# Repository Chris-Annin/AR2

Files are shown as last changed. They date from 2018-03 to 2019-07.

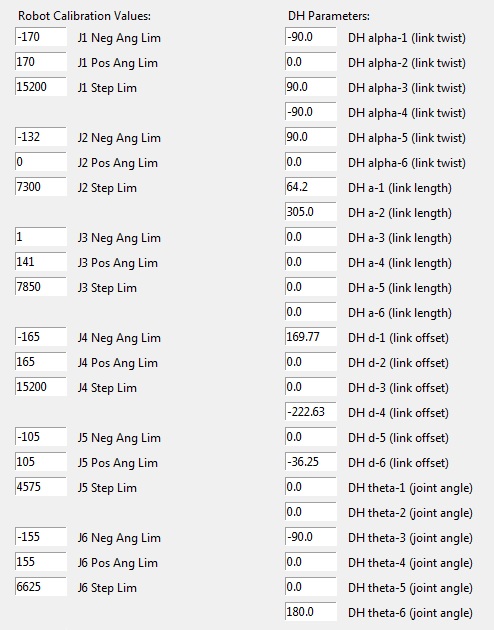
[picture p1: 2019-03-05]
RaspberryPi/default calibration values.jpg

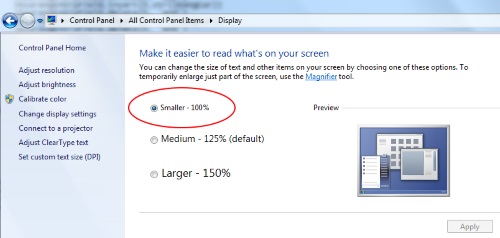
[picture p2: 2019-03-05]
RaspberryPi/display setting.jpg

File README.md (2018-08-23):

# AR2

## 6 axis stepper motor robot and control software

https://www.anninrobotics.com/

The AR2 is a small desktop robot that is modeled similar to an industrial 6 axis robot.  This is a DIY project that can be built from 3D printed components or from machined aluminum components, uses low cost stepper motors and arduino controller.

This project includes:

- Bill of materials and instructions
- CAD files to 3D print components to build the robot
- Arduino sketch for stepper driver control
- Software to program and operate robot
- Kinematic model

All geared stepper motors and drivers are available from  [www.omc-stepperonline.com](https://www.omc-stepperonline.com/?tracking=59c1139e8987b) and all other misc. hardware are off-the-shelf items available from multiple sources (see the bill of materials info within each manual).

(https://www.youtube.com/watch?v=EAcU4k2Qskk)

Startup & Calibration: [Calibration Video](https://youtu.be/MMESgfq2Mjg)

Programming: [Programming Video](https://youtu.be/BozgdjE-HR8)

How the math works: [Kinematic Videos](https://youtu.be/FIx6olybAeQ)

Please review all of the videos on programming and calibration,
I will try to answer as many emails as I can: chris.annin@gmail.com
#
Its important to me that this project is free and available to everyone but any donations that
can help with all that has gone into it would be hugely appreciated.  Thank you very much.


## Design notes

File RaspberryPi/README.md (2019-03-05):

# AR2 Raspberry Pi Source Files
Contributed by Zach Allen

This code is modified from the software version `2.1.5` so you can drive the AR2 Robot with a Raspberry Pi.  You can use a keyboard, mouse, and monitor with the RPi, or configure it as an access point and connect to it remotely from a tablet or phone using VNC Viewer.

### Prerequisites

Make sure you're using a complete version of Raspbian.  This has not been tested on other OS versions.  Find the latest Raspbian distribution at Raspberry Pi's [Download](https://www.raspberrypi.org/downloads/raspbian/) page.

## Getting Started and Installation

Once the files are on your Raspberry Pi, follow the links below to complete the set-up procedure.

1. Follow the [Configure RPi](ref/CONFIGURE.md) guide to clone the GitHub repository to your RPi and to properly set up the configuration settings for the following steps.
2. Follow the [Desktop Shortcut](ref/SHORTCUT.md) guide to add a clickable shortcut to your desktop to easily launch the program.
3. Follow the [Run-on-Boot](ref/RUN-ON-BOOT.md) guide to configure the program to launch automatically when you start the RPi.
4. Follow the [Access Point](ref/AP-SETUP.md) guide to set up your RPi to connect to it remotely, via a phone or tablet using VNC.

## Using the program

Plug the USB into the Raspberry Pi and the Arduino, give power to the Arduino and the AR2, and you will be all set to run the AR2 software.  Please see Chris's [documentation](https://www.anninrobotics.com/downloads) for using the software.

## Built With

* [Raspbian Stretch](https://www.raspberrypi.org/downloads/raspbian/) - The OS used

## Authors

* **Chris Annin** - *Initial work* - [Annin Robotics](https://www.anninrobotics.com/)
* **Zach Allen** - *Modifying software for RPi*

## Acknowledgments

* Huge kudos to Chris Annin for all the work he has done on the AR2, and for sharing it for free for others to learn and create!

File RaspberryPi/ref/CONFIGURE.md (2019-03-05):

# Set Up and Configure your Raspberry Pi
[Return to README.md](../README.md)

## Download Raspbian OS

If you are using a "fresh" Raspberry Pi, you'll need to get an OS on a Micro SD card to use the RPI.  Go to Raspberry Pi's [download](https://www.raspberrypi.org/downloads/raspbian/) page to get the latest Raspbian distribution for Raspberry Pi.  At the time of this writing, the OS is "Raspbian Stretch with desktop and recommended software".  This page also has instructions for writing the OS image to a Micro SD card as well.

## Boot up the Raspberry Pi

Once the OS image is copied onto the Micro SD card, insert the SD card into the RPi, connect a monitor, keyboard and mouse, and plug in 5V power with a micro USB.  The RPi will turn on automatically and begin installing the OS. Once booted, follow the on-screen set-up instructions.

### Configure Settings

Open the applications ("Start") menu and select `Preferences` and then `Raspberry Pi Configuration`.

On the `Interfaces` tab, make sure the following are marked as `Enabled`
* SSH
* VNC
* Serial Port
* Serial Console

If you will be using a tablet for remote control of the RPi, you can change the screen resolution accordingly on the `System` tab.  Once you change the resolution, you will be required to restart the RPi.

## Clone GitHub Repository

Open terminal and navigate to the `Documents` folder.
```
cd /home/pi/Documents/
```

Type the following command to clone the repository
```
git clone https://github.com/Chris-Annin/AR2.git
```

Once it has finished downloading, navigate down into the `RaspberryPi` folder
```
cd /AR2/RaspberryPi
```

The paths in the source code are mapped to this directory.  If you would prefer the source files to be located in a different directory, all of the paths in the `AR2.py` file must be updated. If anyone knows of a better way to use the relative path, please let me know and I'll update the files and this guide.

If you want to check that the program run, type the following command
```
python AR2.py
```

[Continue](./SHORTCUT.md) to create a desktop shortcut to run the program.

[Return to README.md](../README.md)

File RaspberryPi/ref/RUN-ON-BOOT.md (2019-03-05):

# Set up Raspberry Pi to run AR2 Program on Start Up
[Return to README.md](../README.md)

This guide will show you how to configure the RPI to run the AR2 program automatically when the RPi is booted.

First, open terminal.  The working directory is not important at this time.

Edit `/etc/profile` and add a command to run the program.
```
sudo nano /etc/profile
```
Scroll all the way to the bottom and add the following
```
sudo python /home/pi/Documents/AR2/RaspberryPi/AR2.py &
```

It is **critical** you have the ampersand (&) at the end, otherwise your Raspberry Pi will get stuck in a loop when booting.

Once you have added the command, save and exit, and reboot.
```
Ctrl+x
y
Enter
```
```
sudo reboot
```

Once the RPi has rebooted, the AR2 software screen should automatically run. Unless you close the program and need to re-open it, you shouldn't need to use the desktop shortcut.  However it's there anyway!

[Continue](./AP-SETUP.md) to learn how to configure your RPi for remote connection via VNC Viewer.

[Return to README.md](../README.md)

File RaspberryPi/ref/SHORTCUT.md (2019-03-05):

# Create Desktop shortcut
[Return to README.md](../README.md)

This guide will show you how to create a Desktop shortcut from which you can run the program.

Open a terminal window and point the directory to the Desktop
```
cd /home/pi/Desktop/
```

Create a new text file on the Desktop.  Since it does not yet exist, a new file will be automatically created.
```
sudo nano AR2.desktop
```

Type or copy/paste the following into the text file.  This will configure the details necessary to make it a desktop shortcut with an icon.
```
[Desktop Entry]
Name=AR2
Comment=AR2 Robot Control Program
Icon=/home/pi/Documents/AR2/RaspberryPi/AR2.ico
Exec=python /home/pi/Documents/AR2/RaspberryPi/AR2.py
Type=Application
Terminal=false
Categories=None;
```
Then, save and exit
```
Ctrl+x
y
Enter
```

Now, the shortcut should appear on your desktop!

If the shortcut hasn't appeared, reboot your Raspberry Pi.
```
sudo reboot
```

If that still doesn't work, check the spelling of everything and make sure the files are in the correct directory.

If you want the program to start up when you turn on the Raspberry Pi, continue on the [run-on-boot documentation](./RUN-ON-BOOT.md)

[Return to README.md](../README.md)

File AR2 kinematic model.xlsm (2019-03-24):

FORWARD KINAMATICS |  |  |  |  |  |  |  |  |  | INVERSE KINAMATICS
 | IN |  |  |  |  |  | OUT |  |  |  | IN
 | degrees | radians
J1 * ( -170 / 170 ) | 0.01 | 0.0001745329252 |  |  |  | X | 323.0799945 |  |  | X | 323.0799945 | J1 | 0.01
J2 * ( -132 / 0 ) | -90 | -1.570796327 |  |  |  | Y | 0.05638699285 |  |  | Y | 0.05638699285 | J2 | -90
J3 * ( 1 / 140 ) | 90 | 0 |  |  |  | Z | 474.7636732 |  |  | Z | 474.7636732 | J3 | 90
 | 0.01 | 0.0001745329252 |  |  |  | y | -89.98 | -1.570447261 |  | y | -89.98 | J4 | 0.01000000001 | 0.01000000001 | -179.99
 | 0.01 | 0.0001745329252 |  |  |  | p | 90.01 | 1.57097086 |  | p | 90.01 | J5 | 0.009999999984 | 0.009999999984 | -0.009999999984 |  | WRIST CONF. | "F"
 | 0.01 | 3.141767187 |  |  |  | r | -90.00999825 | -1.570970829 |  | r | -90.00999825 | J6 | 0.009999999994 | 0.009999999994 | -179.99 |  | QUADRANT | 1
 | DH params |  |  |  |  |  |  |  |  |  |  |  | CALCULATE J2 AND J3 ANGLE ( note that only arm forward and arm mid are used. Arm back config not used and elbow back is not used - to flip robot center of wrist "P" back past center line of J1 would require arm confuration paramaters be attached to each move command )
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

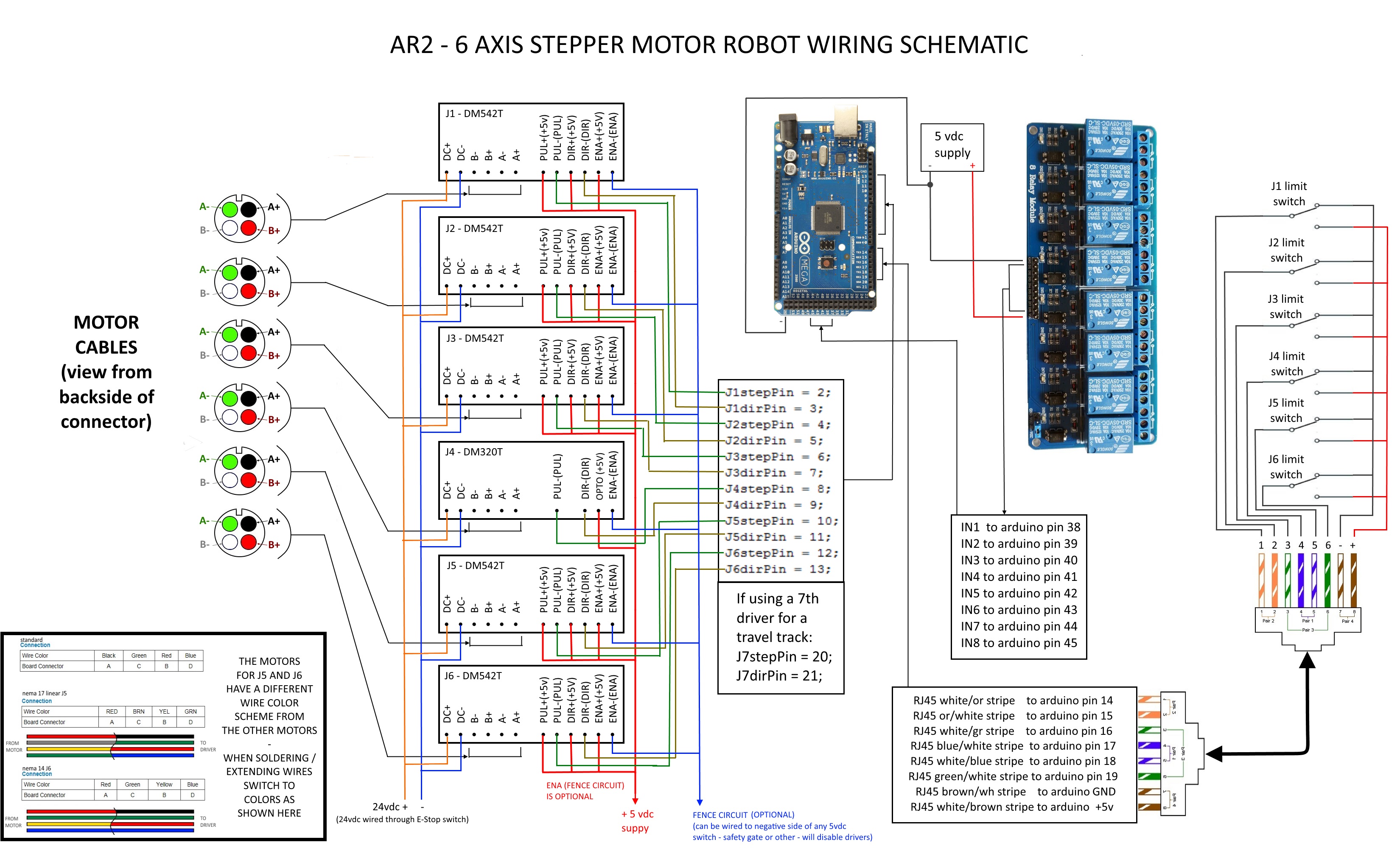
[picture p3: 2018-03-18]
Schematic.jpg

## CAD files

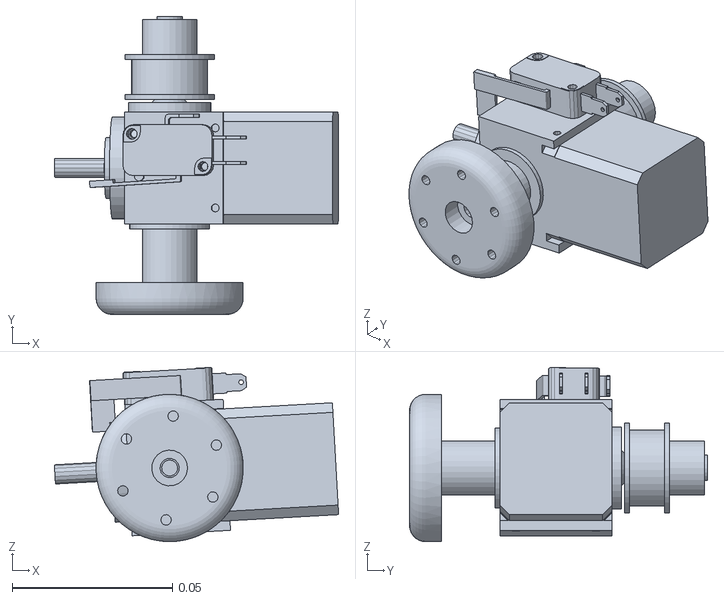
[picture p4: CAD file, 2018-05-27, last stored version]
AR2urdf/meshes/link_5.STL
0.0888 x 0.0931 x 0.0544

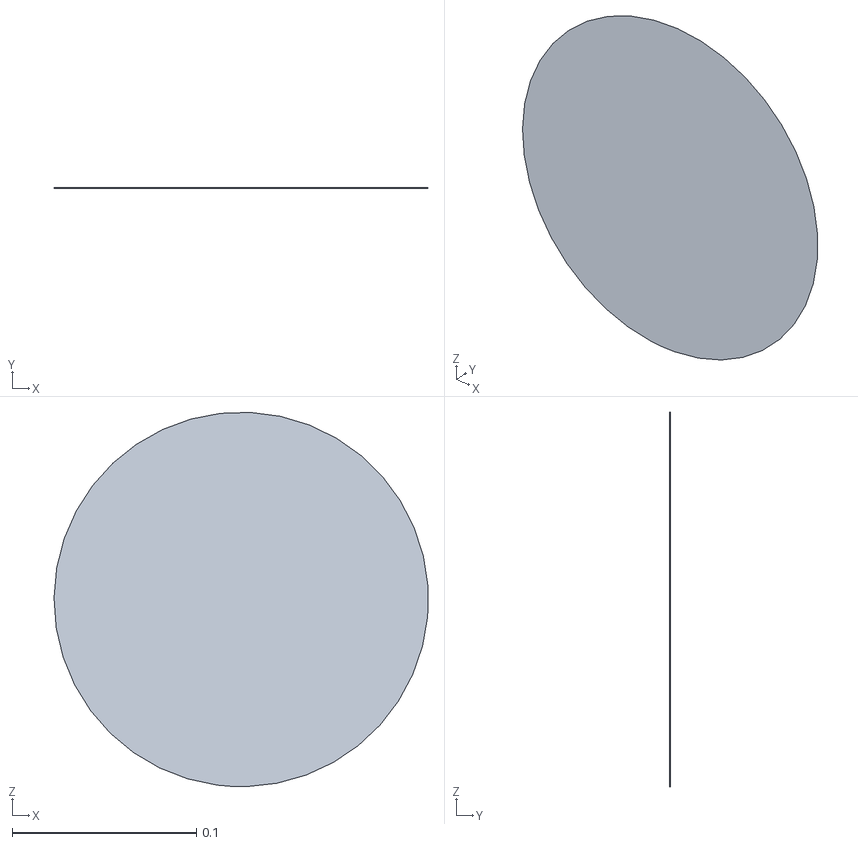
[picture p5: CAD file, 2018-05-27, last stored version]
AR2urdf/meshes/base_link.STL
0.203 x 0.000127 x 0.203

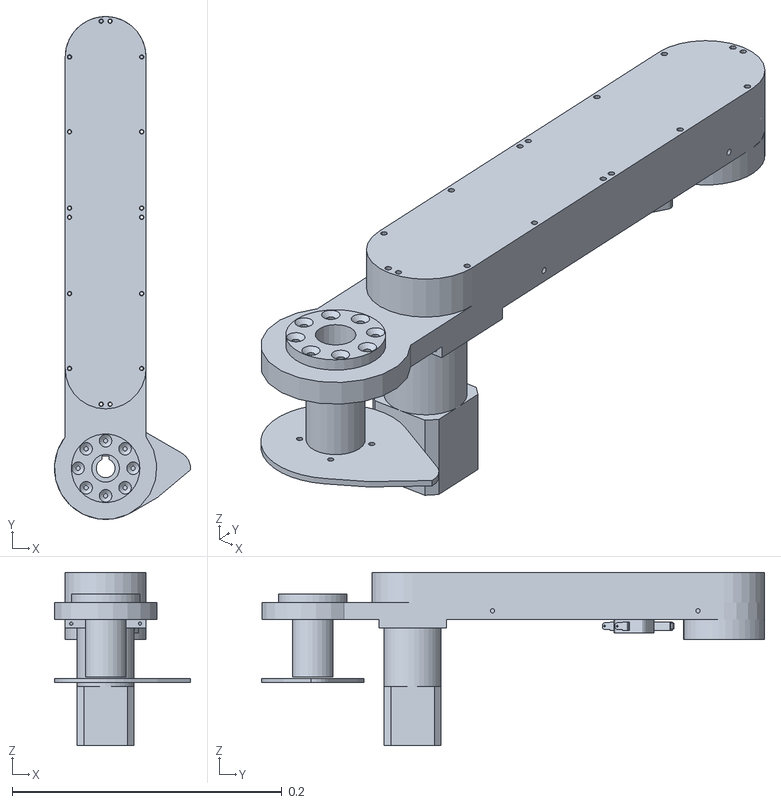
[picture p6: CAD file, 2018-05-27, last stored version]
AR2urdf/meshes/link_2.STL
0.101 x 0.373 x 0.129

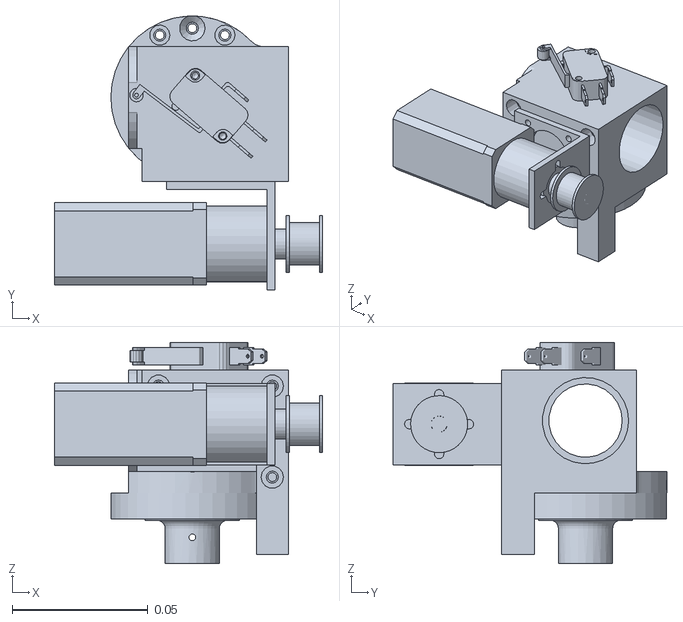
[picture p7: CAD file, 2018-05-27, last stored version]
AR2urdf/meshes/link_3.STL
0.0987 x 0.101 x 0.0816

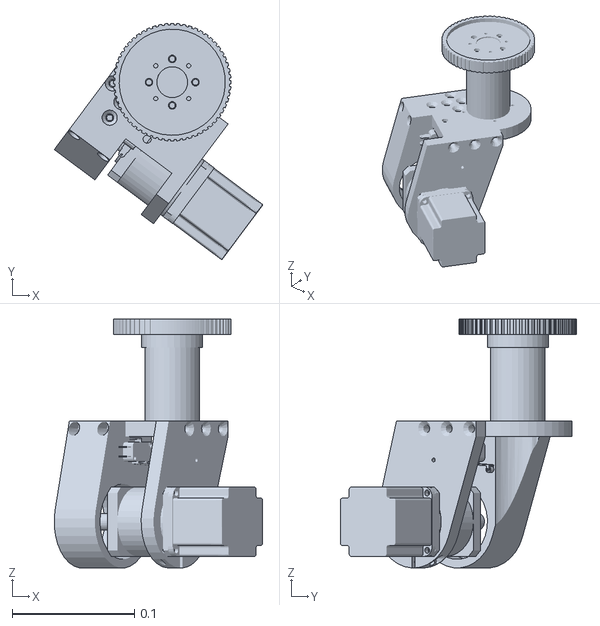
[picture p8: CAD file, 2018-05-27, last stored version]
AR2urdf/meshes/link_1.STL
0.171 x 0.194 x 0.204

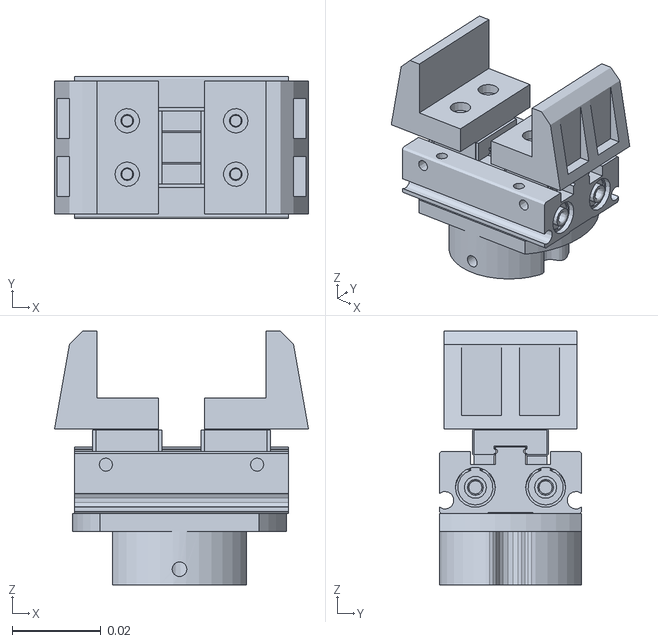
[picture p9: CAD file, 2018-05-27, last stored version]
AR2urdf/meshes/link_6.STL
0.0571 x 0.032 x 0.057

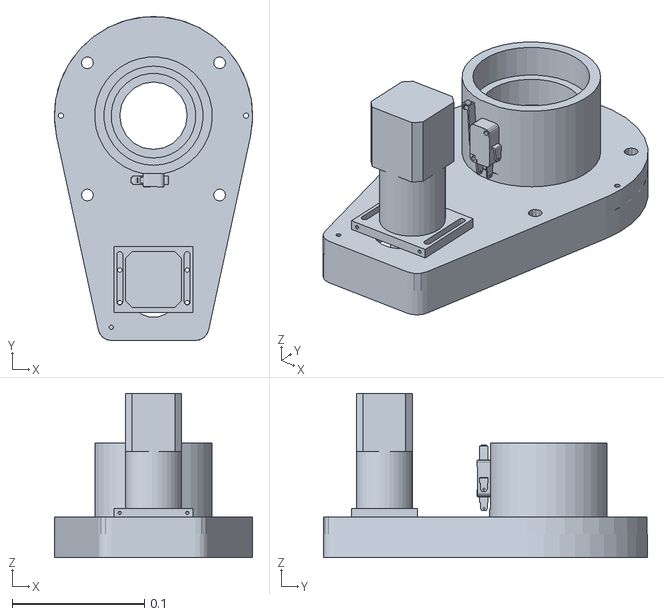
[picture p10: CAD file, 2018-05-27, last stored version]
AR2urdf/meshes/robot_base.STL
0.15 x 0.245 x 0.124

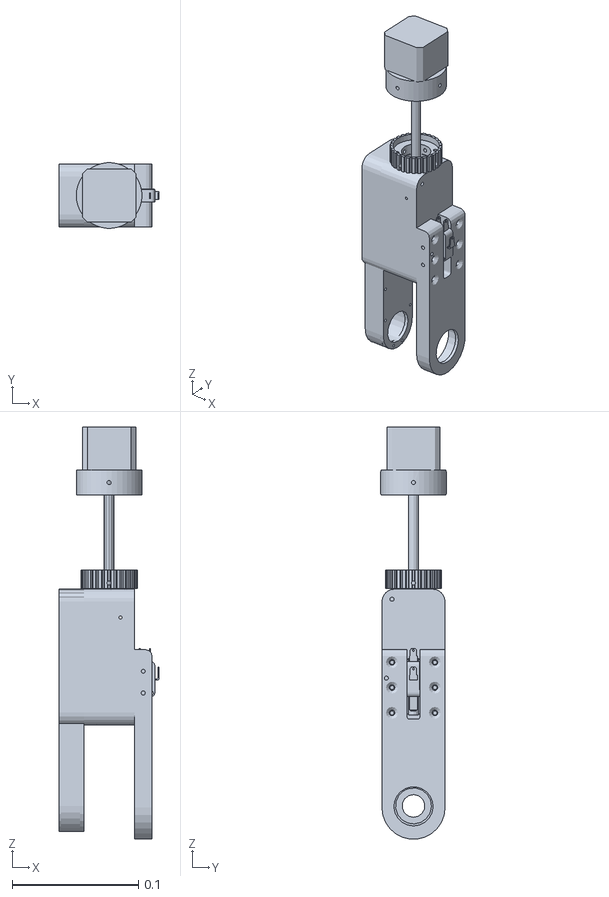
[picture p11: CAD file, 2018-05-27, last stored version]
AR2urdf/meshes/link_4.STL
0.0793 x 0.052 x 0.326

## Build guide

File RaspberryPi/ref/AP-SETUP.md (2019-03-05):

# Set up Access Point
[Return to README.md](../README.md)

### Content Attribution
This method is from the [Raspberry Pi documentation](https://www.raspberrypi.org/documentation/configuration/wireless/access-point.md) on setting up a wireless access point.  Much of the content is identical, but it has been adapted for use by beginners.  The parts directly copied from the documentation are shown in quotation level.
**Setting up the RPi as an access point only works if you have wireless capability on your Raspberry Pi.**

Wireless functionality is currently available on the following devices:
* Raspberry Pi Zero W
* Raspberry Pi 3
* Raspberry Pi 2 + AP-capable WiFi Dongle

Additional RPi devices may support this method, but the aforementioned devices have been tested and are confirmed to work.

### Getting Started

> Use the following to update your Raspbian installation:
> ```
> sudo apt-get update
> sudo apt-get upgrade
> ```
>
> Install all the required software in one go with this command:
> ```
> sudo apt-get install dnsmasq hostapd
> ```
>
> Since the configuration files are not ready yet, turn the new software off as follows:
> ```
> sudo systemctl stop dnsmasq
> sudo systemctl stop hostapd
> ```
>
> To ensure that an updated kernel is configured correctly after install, reboot:
> ```
> sudo reboot
> ```

### Configuring a static IP

> We are configuring a standalone network to act as a server, so the Raspberry Pi needs to have a static IP address assigned to the wireless port. This documentation assumes that we are using the standard 192.168.x.x IP addresses for our wireless network, so we will assign the server the IP address 192.168.4.1. It is also assumed that the wireless device being used is wlan0.
>
> To configure the static IP address, edit the dhcpcd configuration file with:
> ```
> sudo nano /etc/dhcpcd.conf
> ```
>
> Go to the end of the file and edit it so that it looks like the following:
> ```
> interface wlan0
>   static ip_address=192.168.4.1/24
>   nohook wpa_supplicant
> ```

To save and exit the editor window, press `Ctrl+x` (which is indicated at the bottom by `^x`), type `y` to save, and then press `Enter`.

> Now restart the dhcpcd daemon and set up the new wlan0 configuration:
> ```
> sudo service dhcpcd restart
> ```

####  Configuring the DHCP server (dnsmasq)

> The DHCP service is provided by dnsmasq. By default, the configuration file contains a lot of information that is not needed, and it is easier to start from scratch. Rename this configuration file, and edit a new one:
> ```
> sudo mv /etc/dnsmasq.conf /etc/dnsmasq.conf.orig  
> sudo nano /etc/dnsmasq.conf
> ```
>
> Type or copy the following information into the dnsmasq configuration file and save it:
> ```
> interface=wlan0      # Use the require wireless interface - usually wlan0
> dhcp-range=192.168.4.2,192.168.4.20,255.255.255.0,24h
> ```

Save and exit:
```
Ctrl+x
y
Enter
```

> So for wlan0, we are going to provide IP addresses between 192.168.4.2 and 192.168.4.20, with a lease time of 24 hours. If you are providing DHCP services for other network devices (e.g. eth0), you could add more sections with the appropriate interface header, with the range of addresses you intend to provide to that interface.
>
> There are many more options for dnsmasq; see the [dnsmasq documentation](http://www.thekelleys.org.uk/dnsmasq/doc.html) for more details.

### Configuring the access point host software (hostapd)

> You need to edit the hostapd configuration file, located at `/etc/hostapd/hostapd.conf`, to add the various parameters for your wireless network. After initial install, this will be a new/empty file.
> ```
> sudo nano /etc/hostapd/hostapd.conf
> ```
>
> Add the information below to the configuration file. This configuration assumes we are using channel 7, with a network name of Robot, and a password robotcontrol. Note that the name and password should not have quotes around them. The passphrase should be between 8 and 64 characters in length.
>
> To use the 5 GHz band, you can change the operations mode from hw_mode=g to hw_mode=a. Possible values for hw_mode are:
>
> ```
> a = IEEE 802.11a (5 GHz)
> b = IEEE 802.11b (2.4 GHz)
> g = IEEE 802.11g (2.4 GHz)
> ad = IEEE 802.11ad (60 GHz).
> interface=wlan0
> driver=nl80211
> ssid=Robot
> hw_mode=g
> channel=7
> wmm_enabled=0
> macaddr_acl=0
> auth_algs=1
> ignore_broadcast_ssid=0
> wpa=2
> wpa_passphrase=robotcontrol
> wpa_key_mgmt=WPA-PSK
> wpa_pairwise=TKIP
> rsn_pairwise=CCMP
> ```

Save and exit:
```
Ctrl+x
y
Enter
```

> We now need to tell the system where to find this configuration file.
> ```
> sudo nano /etc/default/hostapd
>```
>
> Find the line with #DAEMON_CONF, and replace it with this:
> ```
> DAEMON_CONF="/etc/hostapd/hostapd.conf"
> ```
>

### Start it up

> Now start up the remaining services:
> ```
> sudo systemctl start hostapd
> sudo systemctl start dnsmasq
> ```

> Add routing and masquerade
> Edit `/etc/sysctl.conf` and uncomment this line:
> ```
> net.ipv4.ip_forward=1
> ```

Save and exit:
```
Ctrl+x
y
Enter
```

> Add a masquerade for outbound traffic on eth0:
> ```
> sudo iptables -t nat -A  POSTROUTING -o eth0 -j MASQUERADE
> ```
>
> Save the iptables rule.
> ```
> sudo sh -c "iptables-save > /etc/iptables.ipv4.nat"
> ```
>

> Edit '/etc/rc.local'.
> ```
> sudo nano /etc/rc.local
> ```
>
> Add this just above "exit 0" to install these rules on boot.
> ```
> iptables-restore < /etc/iptables.ipv4.nat
> ```

Save and exit:
```
Ctrl+x
y
Enter
```

> Reboot
```
sudo reboot
```

> Using a wireless device, search for networks. The network SSID you specified in the hostapd configuration should now be present, and it should be accessible with the specified password.
>
> If SSH is enabled on the Raspberry Pi access point, it should be possible to connect to it from another Linux box (or a system with SSH connectivity present) as follows, assuming the pi account is present:
> ```
> ssh pi@192.168.4.1
> ```
>
> By this point, the Raspberry Pi is acting as an access point, and other devices can associate with it. Associated devices can access the Raspberry Pi access point via its IP address for operations such as rsync, scp, or ssh.

To connect to your Raspberry Pi from a phone or tablet, download the VNC Viewer app.  Add a device using the RPi's IP address `192.168.4.1` and give it a name such as `Robot`.  Then, type in the RPi's credentials as you've set them up.  If the connection is successful, you should be able to see the RPi's screen and control it remotely.

Congrats, you're all set up to use the AR2 software remotely!  If you have any troubles with this tutorial, please file an issue on the GitHub page and we'll try to get it resolved ASAP.

[Return to README.md](../README.md)

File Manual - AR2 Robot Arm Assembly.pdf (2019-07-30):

# Model AR2 Assembly Manual

Mechanical Unit Assembly
Manual | 1

# NOTE:

### This manual shows the construction of the AR2 robot using aluminum for the primary structural components, and plastic for the belt covers and spacer

components. Use Loctite on all screws during assembly process.

This robot can also be constructed using 3D printed components. The .stl print files for all components can be found on the project page. The construction illustrated in this manual is the same using either aluminum or 3D printed components - note the following details if using 3D printed components:

### - 3D printed components require all threaded holes to be cleared with

appropriate drill size and then tapped.

### - All printed components were printed at minimum 50% solid with the exception of any drive spindles and tension rings which were printed at

90%+ solid. Parts were printed at 2mm layer height and thick shells.

### - The J1 baseplate, J1 baseplate spacer and J2 arm larger than most 3D printer beds and therefore are printed in 2 pieces and require being epoxied

together.

### - The printed design calls for additional reinforcements to be epoxide in place around the J1 base and at the base of the J2 arm (see details at the end of this manual) - You will need to cut and drill aluminum tubing as shown in BOM section of

this manual.

# BEARING FIT:

The CAD models for the AR2 robot are sized for a slight press fit on all bearing and race diameters. The assembly steps in this manual also reference pressing the bearings and races in place. Given customer feedback and the fact that most don’t have access to a quality bearing press or hardware we have tried to make sure the aluminum kits we offer are closer to a slip fit. If bearings get improperly wedged or tilted and then attempt to press, severe damage can occur. Given the opportunity for bearings to jam and permanently damage to occur we have opted to try and provide kits that error on the side of a looser fit to avoid part damage and frustration. If the tolerance stack up on your components results in a race that can slightly spin please use a small strip of shim stock or wax paper

to alleviate any movement. A small dab of epoxy can also be used.

### The bearing oil that comes on bearings should be sufficient lubrication given the low speed and pressure of the robot joints. If additional lubrication is

needed a very small about of white lithium grease is recommended.

# BILL OF MATERIALS

# Structural Components

## Parts shown are made from aluminum but you can also 3D print the

structural components if you are building a fully 3D printed robot.

## (see note below on J4 main shaft as this part cannot be 3D printed)

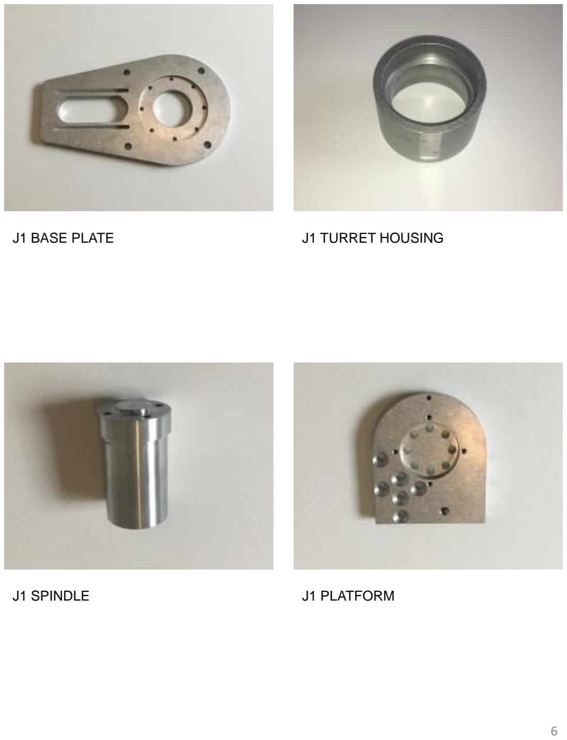
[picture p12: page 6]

J1 BASE PLATE | J1 TURRET HOUSING
J1 SPINDLE | J1 PLATFORM

J2 TURRET HOUSING | J2 ARM
J2 DRIVE SPINDE | J2 TENSION RING

J1 & J3 MOTOR MOUNT | J2 MOTOR SUPPORT
J3 BEARING CUP | J3 SPINDLE

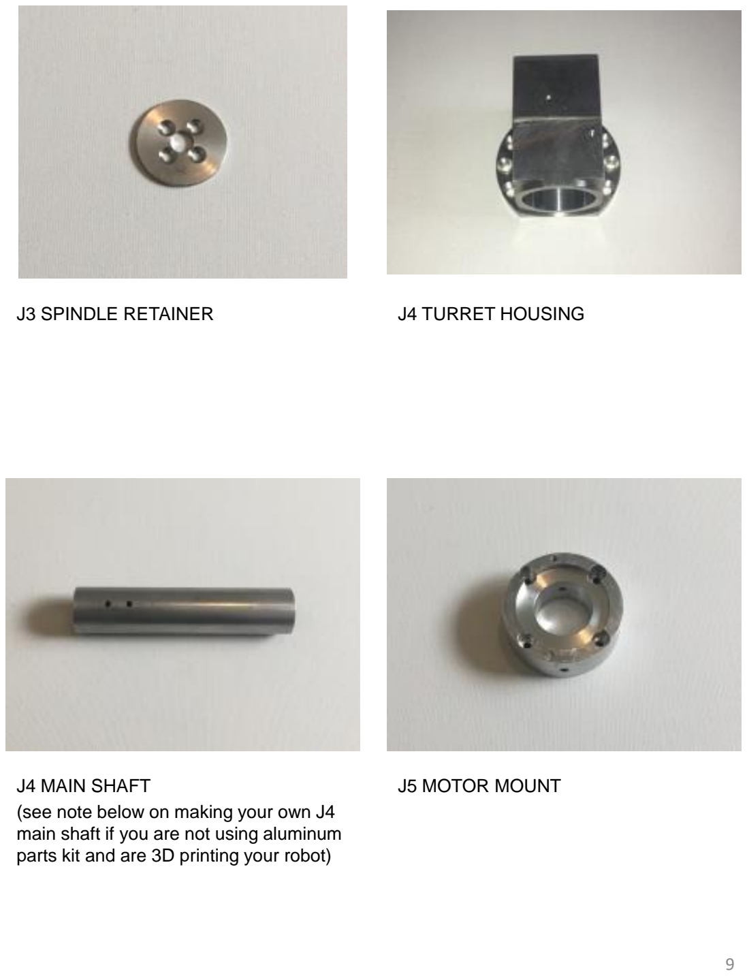
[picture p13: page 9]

J3 SPINDLE RETAINER | J4 TURRET HOUSING

J4 MAIN SHAFT
(see note below on making your own J4 main shaft if you are not using aluminum parts kit and are 3D printing your robot)

J5 MOTOR MOUNT

J4 TIMING HUB | J4 MOTOR MOUNT
J5 HOUSING | J5 BELT CARRIER & J5 BELT CARRIER CLAMP

J5 BEARING POST | J5 IDLER TENSION BLOCK
J6 MAIN BEARING ARM | J6 HOUSING SINGLE PIECE

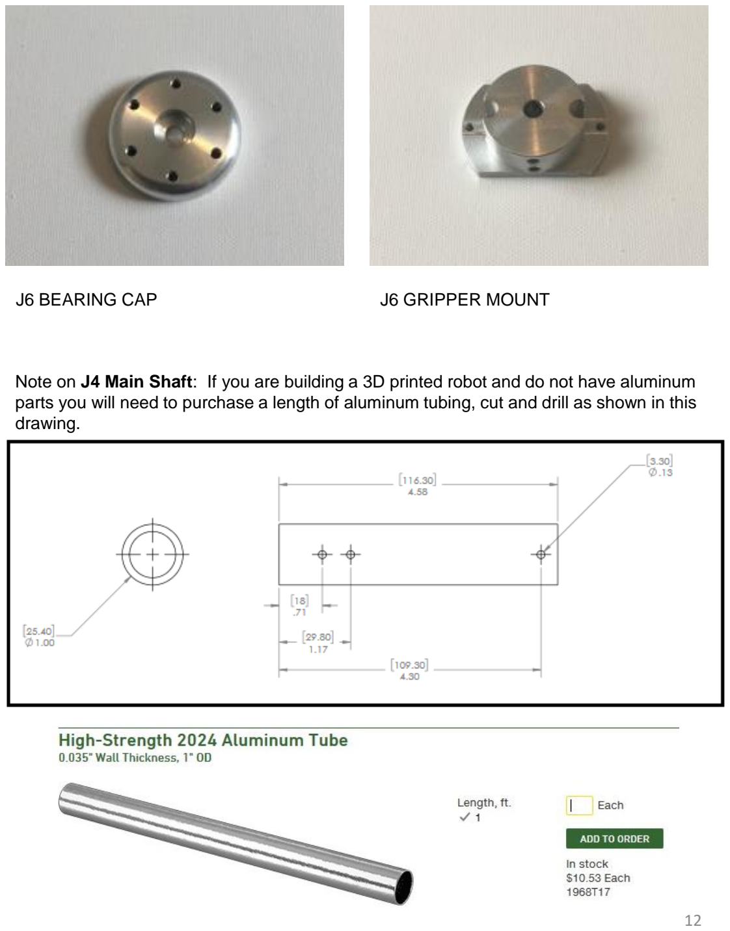
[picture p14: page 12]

J6 BEARING CAP | J6 GRIPPER MOUNT

Note on J4 Main Shaft: If you are building a 3D printed robot and do not have aluminum parts you will need to purchase a length of aluminum tubing, cut and drill as shown in this drawing.

# 3D Printed Covers and Spacers

J1 BASE SUPPORT SPACER PART 1 | J1 BASE SUPPORT SPACER PART 2
J2 ARM COVER SPACER (x2) | J2 SIDE COVER (x2)

J5 SIDE COVER CAP | J5 SIDE COVER
J5 SIDE COVER SPACER (x2) | J6 LIMIT SWITCH TIP

# Stepper Motors

# Geared and linear stepper motors as well as stepper drivers are available from Stepper Online http://www.omc-stepperonline.com/

### J1 motor SKU: 17HS15-1684S-HG20

### J2 motor SKU: 23HS22-2804S-HG50

### J3 motor SKU: 17HS15-1684S-HG50

### J4 motor SKU: 11HS20-0674S-PG14

### J5 motor SKU: 17LS19-1684E-200G

### J6 motor SKU: 14HS13-0804S-PG19

### J4 bracket SKU: ST-M3

# Hardware Components

Qty. (2) for J1 bearings - Amazon | Qty. (2) for J2 bearings - Amazon
Qty. (1) for J3 bearing - Amazon | Qty. (1) 35mm thrust bearing and washer set for J3 - Amazon

Qty.(3) 1” thrust bearings (2 for J4 and 1 for J6) –McMaster Carr

Qty.(4) (3 for J4 and 1 for J6) –McMaster Carr

Qty. (1) for J5 belt idler - Amazon | Qty.(1) set of 10 shafts (you only need 2) - Amazon

Qty.(2) (1 for J4 and 1 for J6) –McMaster Carr

Qty.(2) for J4 bearings - Amazon

Qty.(1) set of 8 bearings (you only need 4)
- Amazon

Qty.(1) set of 10 8x16x5mm bearings (you only need 1) - Amazon

Qty.(1) for J6 bearing - Amazon

Qty. (1) J1 belt - Amazon | (2’ length) J3 chain – McMaster Carr
Qty.(1) link for J3 – McMaster Carr | Qty.(1) J4 belt – Amazon
Qty.(1) J5 belt – Amazon | Qty.(1) driven pulley for J1 – Amazon

Qty.(2) 15 tooth 8mm bore sprocket (1 for J1 and 1 for J6) - Ebay

Qty.(1) for J4 - Ebay

Qty.(2) for J3 chain – McMaster Carr

Qty.(1) McMaster Carr

Qty.(1) McMaster Carr
Aluminum parts kit comes with this tube

Qty.(1) – McMaster Carr

Qty.(1) – McMaster Carr

M3x10 SET SCREW | 3
M3x14 SOCKET HEAD CAP SCREWS | 20
M3x18 SOCKET HEAD CAP SCREWS | 4
M3x20 FLAT HEAD SCREWS | 6
M3x25 SOCKET HEAD SCREWS | 16
M3x3 SET SCREW | 4
M3x4 SET SCREW | 1
M3x5 SOCKET HEAD CAP SCREW | 1
M3x6 SET SCREW | 10
M3x8 SOCKET HEAD CAP SCREW | 6
M4 nuts | 4
M4 washers | 12
M4x10 FLAT HEAD SCREWS | 16
M4x10 SET SCREWS | 9
M4x10 SOCKET HEAD CAP SCREWS | 18
M4x14 FLAT HEAD SCREW | 2
M4x18 FLAT HEAD SCREW | 6
M4x20 SOCKET HEAD CAP SCREWS | 8
M4x35 SOCKET PHIPIPS PAN HEAD SCREWS (fully threaded) | 4
M4x5 SET SCREWS | 22
M6x14 SOCKET HEAD CAP SCREWS | 13
M6x18 FLAT HEAD SCREWS | 9
M6x20 SOCKET HEAD CAP SCREWS | 3
M8x25 SQUARE HEAD | 1

# Gripper & Switches

### Pneumatic Gripper – Ebay (used)

### 24vdc Solenoid to actuate gripper – Amazon

### NOTE: solenoid valves tend to interrupt the serial connection to the Arduino if located too close. If you find Arduino losing connection when valve actuates

install a flyover diode across solenoid terminals (reverse bias).

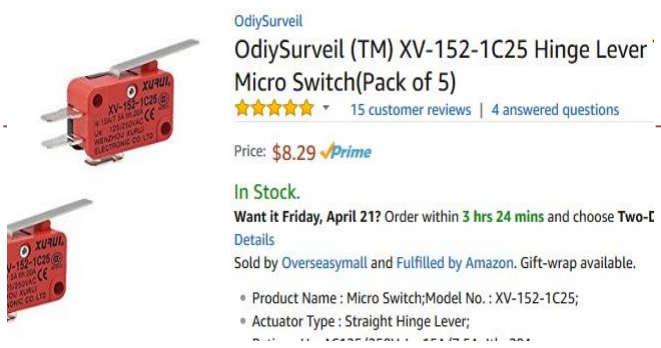
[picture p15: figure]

Qty.(5 switches) – Amazon | Qty.(1 switch) – Amazon

# ASSEMBLY

Cut motor pigtails and attach JST connectors to each of the 6 motors as shown in section 4 of the wiring harness manual.

Fabricate 6 limit switch pigtails with JST connectors as shown in section 3 of the wiring harness manual.

Press (x2) #32009 bearing races into the J1 turret housing. If you do not have access to a press place turret housing in oven @ 350° and bearing races in freezer for 60 minutes, quickly remove housing from oven – the cold races will drop into the expanded housing. (you will need to do this for both races one at a time)

Install #32009 bearing on J1 spindle as shown.

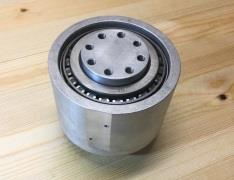
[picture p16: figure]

Insert J1 spindle into turret housing then install the other #32009 bearing on top side of spindle. (note location of flat on housing)

Press (x2) #30206 bearing races into the J2 turret housing. If you do not have access to a press place turret housing in oven @ 350° and bearing races in freezer for 60 minutes, quickly remove housing from oven – the cold races will drop into the expanded housing. (you will need to do this for both races one at a time)

Use abrasive saw to cut square M8 screw down as shown leaving approx 8mm of threads remaining.

Install square head M8 screw into J1 turret platform as shown – make sure square head is tangent to center bolt circle as indicated by dashed line in picture.

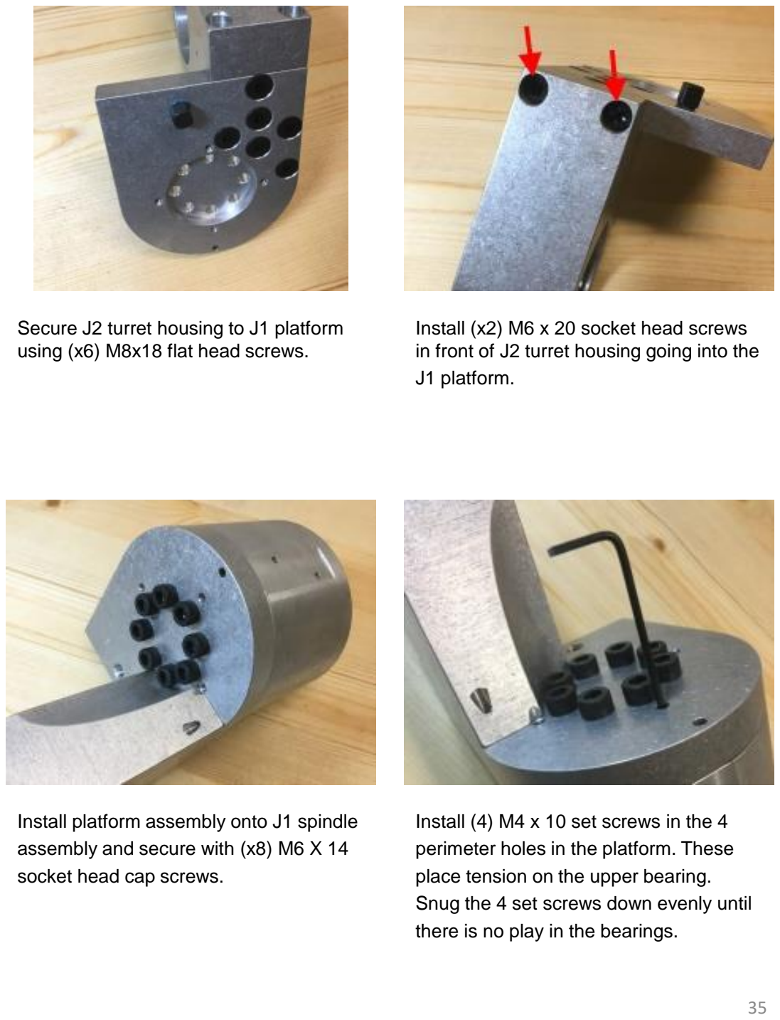
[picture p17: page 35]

Secure J2 turret housing to J1 platform using (x6) M8x18 flat head screws.

Install (x2) M6 x 20 socket head screws in front of J2 turret housing going into the J1 platform.

Install platform assembly onto J1 spindle assembly and secure with (x8) M6 X 14 socket head cap screws.

Install (4) M4 x 10 set screws in the 4 perimeter holes in the platform. These place tension on the upper bearing. Snug the 4 set screws down evenly until there is no play in the bearings.

Mount J2 limit switch to J2 housing using (x2) M3x14 socket head cap screws.

Install the J1 assembly onto the J1 base as shown. Make sure the flat
surface with 2 holes is facing toward the back.

Secure J1 assembly from the bottom using (x8) M4x10 socket head cap screws.

Mount J1 limit switch to J1 housing using (x2) M3x14 socket head cap screws.

Install the J1 driven sprocket onto the J1 spindle and secure with (x4) M6x14 socket head cap screws.

Install J1 motor mount onto J1 motor using (x4) M4x10 flat head screws and then Install XL15 tooth 8mm bore drive sprocket on J1 gear motor shaft.

NOTE: you can broach pulley for keyway or remove key from motor shaft with pliers or vise grip and use setscrew.

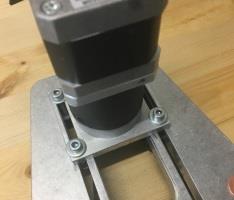
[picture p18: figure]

Install motor assembly onto base and secure with (4) 4mm X 20 socket head cap screws and (4) 4mm washers. Make sure (2) 3mm tension holes located on ends of slots are facing toward back. (note this picture was taken with a prototype slotted J1 baseplate – print files and future parts will have fixed mounting holes in J1 baseplate – new pictures will be taken)

Tension J1 belt using (x2) M3x10 set screws in rear of motor mount slots. (note this picture was taken with a prototype slotted J1 baseplate – print files and future parts will have fixed mounting holes in J1 baseplate – new pictures will be taken)

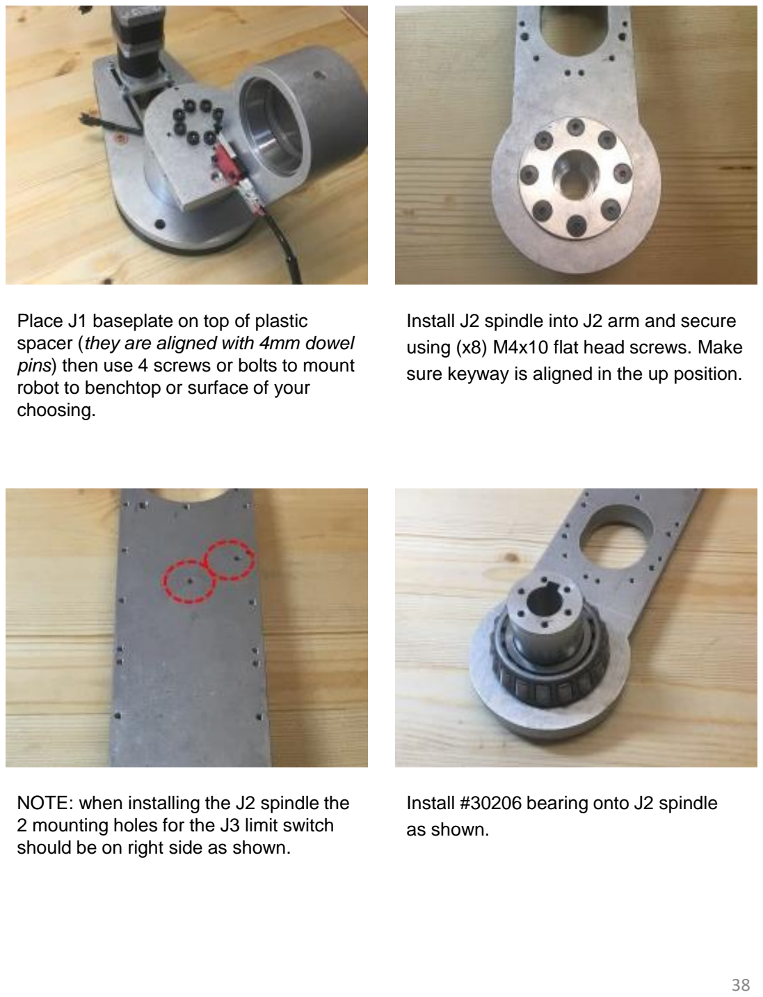
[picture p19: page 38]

Place J1 baseplate on top of plastic spacer (they are aligned with 4mm dowel pins) then use 4 screws or bolts to mount robot to benchtop or surface of your choosing.

Install J2 spindle into J2 arm and secure using (x8) M4x10 flat head screws. Make sure keyway is aligned in the up position.

NOTE: when installing the J2 spindle the 2 mounting holes for the J3 limit switch should be on right side as shown.

Install #30206 bearing onto J2 spindle as shown.

Install M3x10 set screw into J2 spindle as shown but do not thread through to keyway yet.

Install J2 arm assembly into J2 turret housing and then install the other #30206 bearing from opposite side as shown.

Install the J2 tension ring and secure with (6) M3 x 10 flat head screws. Note orientation – tension ring is 90° to the J2 arm.

Install and snug (x4) M4x5 screws until there is no play in J2 bearings.

Remove (x4) M4 cap screws from the J2 motor gearbox as shown.

Remove the top of the gearbox as shown.

Install the J2 motor support plate over the gearbox housing as shown.

Reinstall the top of the J2 gearbox and re-secure with M4 cap screws. (make sure the key is in the up position as shown)

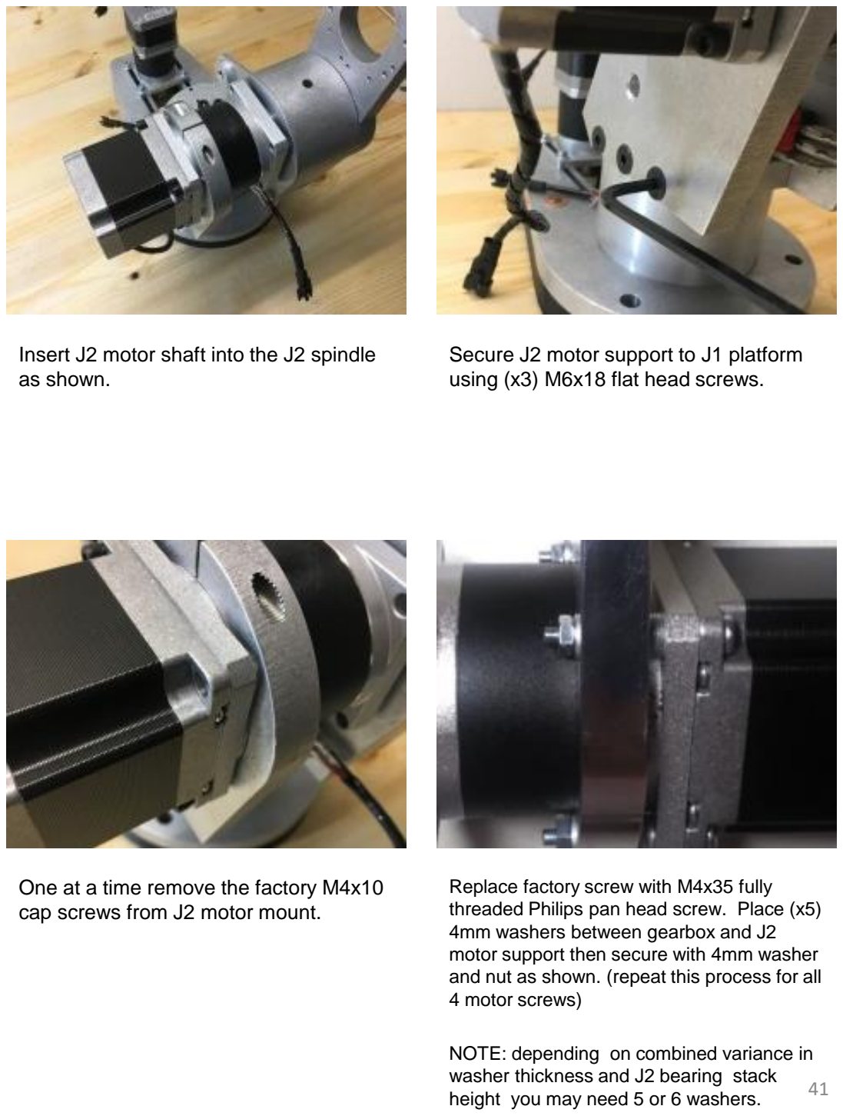
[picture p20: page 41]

Insert J2 motor shaft into the J2 spindle as shown.

Secure J2 motor support to J1 platform using (x3) M6x18 flat head screws.

One at a time remove the factory M4x10 cap screws from J2 motor mount.

Replace factory screw with M4x35 fully threaded Philips pan head screw. Place (x5) 4mm washers between gearbox and J2 motor support then secure with 4mm washer and nut as shown. (repeat this process for all 4 motor screws)

NOTE: depending on combined variance in washer thickness and J2 bearing stack height you may need 5 or 6 washers.

Install and snug M6x20 cap screw in J2 motor support plate.

NOTE: do not overtighten and deform gear box. This only needs to be tight enough to locate gearbox radially and prevent it from rotating.

Tighten M3x10 set screw through access hole in J2 turret housing as shown.

Install J3 motor mount onto J3 motor using (x4) M4x10 flat head screws.

The 13 tooth 8mm bore sprockets must be drilled and tapped to accept a 4mm set screw. Use a 3.3mm (#29) drill to drill 2 holes in each sprocket.
(holes should be 90 from each other)

Use 4mm tap to thread (2) holes in each sprocket (total 4 holes)

Install sprocket on to J3 motor shaft and tighten (x2) M4x5 set screws.

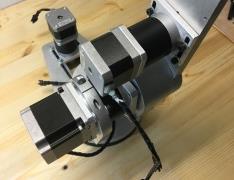
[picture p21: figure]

Install J3 motor onto J2 arm and secure with (x4) M4x20 socket head cap screws.

Mount J3 limit switch to J2 arm using (x2) M3x14 socket head cap screws.

Press (1) #30204 bearing race into the J3 bearing cup.

Secure J3 bearing cup and race to end of J2 arm using (6) M3 x 25 flat head screws.

Use abrasive saw to cut length of 8mm keyed shaft – length should be between 50mm & 53mm long.

Use abrasive saw to cut length of 2mm keyed stock to 25mm long.

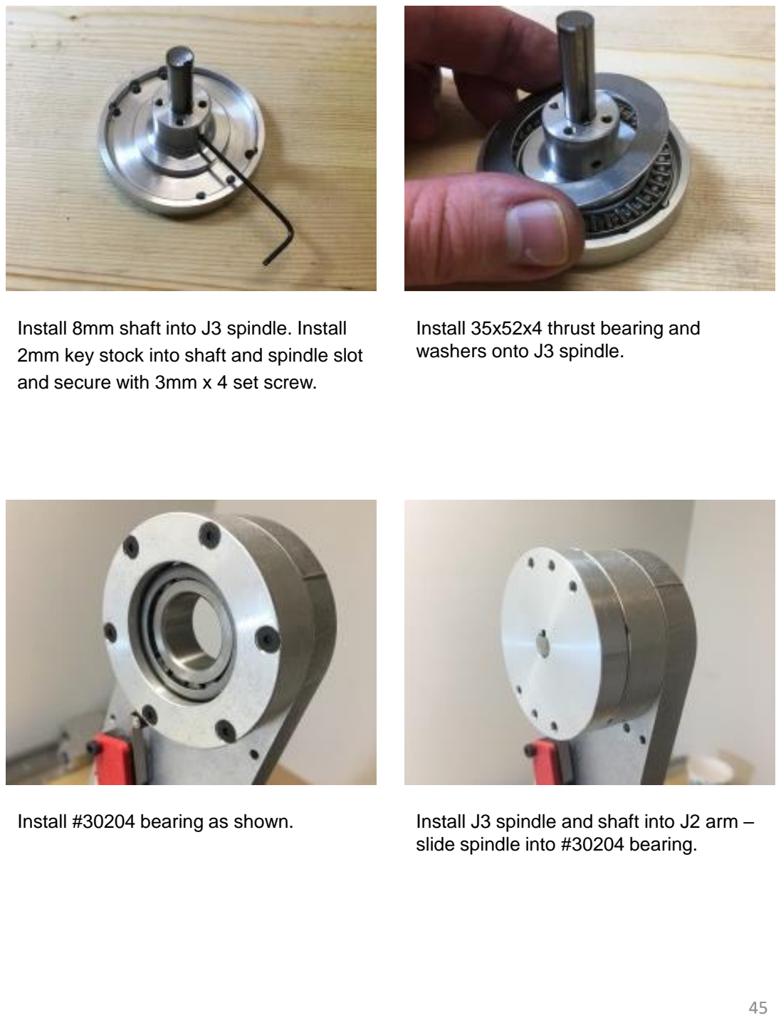
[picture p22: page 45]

Install 8mm shaft into J3 spindle. Install 2mm key stock into shaft and spindle slot and secure with 3mm x 4 set screw.

Install 35x52x4 thrust bearing and washers onto J3 spindle.

Install #30204 bearing as shown. | Install J3 spindle and shaft into J2 arm – slide spindle into #30204 bearing.

Install J3 spindle retainer. Secure with (4) M3 x 10 flat head screws. Tension screws so there is no play in bearings.

Install one sprocket on the J3 spindle Shaft and secure with (x2) M4x5 set screws.

Cut length of 04B roller chain down to 20-3/4” long (52.7 cm). It should have 43 links.

Install master link in 04B roller chain.

Install chain around J3 and motor sprockets.

Leave J3 motor mount screws barely snug so motor can still slide and then install (x2) M3x14 cap screws into lower holes on motor mount and then tighten to tension the chain. (these M3 screws will push against the lower motor mount screws)

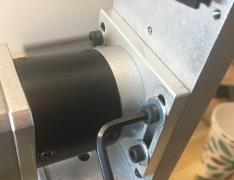
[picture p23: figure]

Once chain has good tension tighten all 4 of the J3 motor mount cap screws.

Press (2) B-1616 (1” ID) needle roller bearings into the J3 turret housing (install one each side).

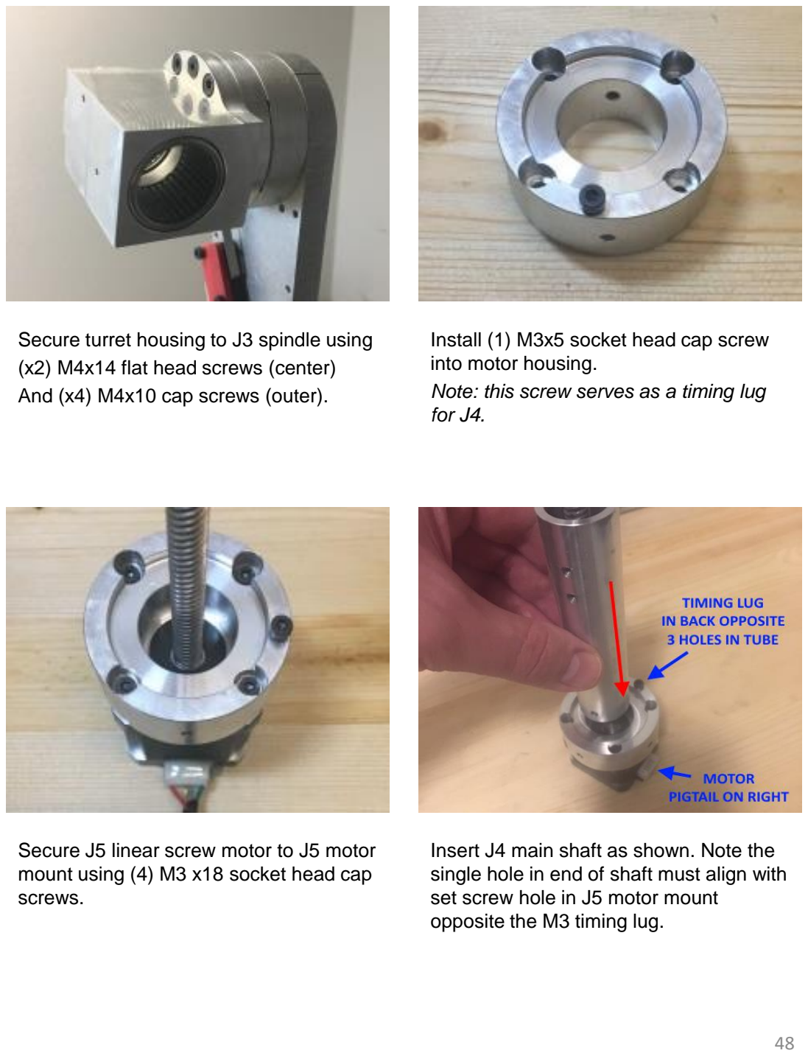
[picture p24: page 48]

Secure turret housing to J3 spindle using (x2) M4x14 flat head screws (center) And (x4) M4x10 cap screws (outer).

Install (1) M3x5 socket head cap screw into motor housing.
Note: this screw serves as a timing lug for J4.

Secure J5 linear screw motor to J5 motor mount using (4) M3 x18 socket head cap screws.

Insert J4 main shaft as shown. Note the single hole in end of shaft must align with set screw hole in J5 motor mount opposite the M3 timing lug.

Install M4x10 set screw as shown – make sure set screw aligns and screws into hole in shaft – note when looking down tube you should be able to see the head of set screw just poking through tube.

Install and snug one more M4 set screw in housing in next hole 90° to the set screw in the previous step.

Install (x1) .032” thick bearing washer over tube and into motor mount as shown.

Install (x1) 1” ID needle bearing over tube and into motor mount as shown.

Install (1) .032” bearing washer over tube and on top of needle bearing as shown.

Insert J5 Motor shaft assembly into J3 turret housing as shown.

Pre install (x4) M4x5 set screws in back side of J4 timing hub.

NOTE: this manual shows the use of a 3D printed timing hub – the kit provided on the website now includes an aluminum timing hub.

Install (x1) .032” bearing washer into timing hub as shown.

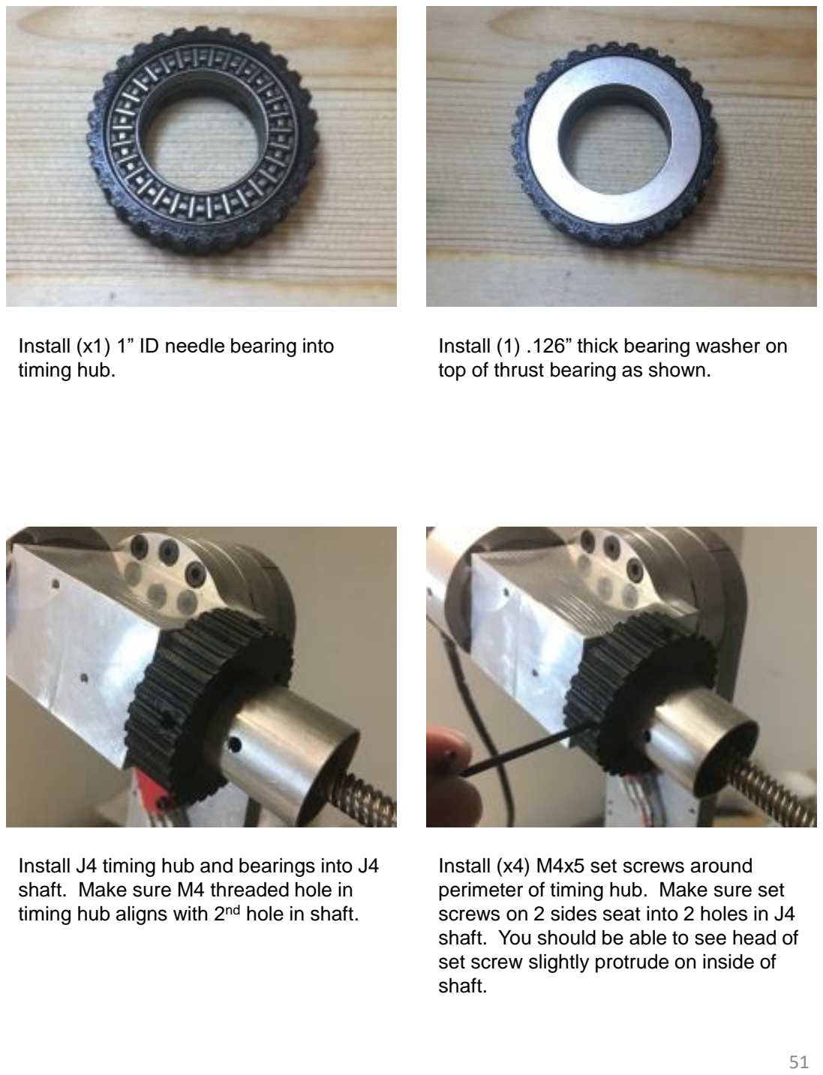
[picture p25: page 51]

Install (x1) 1” ID needle bearing into timing hub.

Install (1) .126” thick bearing washer on top of thrust bearing as shown.

Install J4 timing hub and bearings into J4 shaft. Make sure M4 threaded hole in timing hub aligns with 2nd hole in shaft.

Install (x4) M4x5 set screws around perimeter of timing hub. Make sure set screws on 2 sides seat into 2 holes in J4 shaft. You should be able to see head of set screw slightly protrude on inside of shaft.

Tighten (x4) M4x5 set screws in face of timing hub to set tension on J4 bearings.

Install J4 motor mount / limit switch contact block as shown and secure with (x3) M4x10 socket head cap screws.

Install Nema11 motor mount bracket and secure with (x4) M3x14 socket head cap screws.

Install J4 motor into bracket and secure with (4) M3x8 socket head cap screws.

Slide XL 10 tooth 6mm bore drive pulley onto motor shaft along with 84XL037 timing belt simultaneously over J4 driven sprocket.

(the belt in these instructions happens to be clear but depending on source will likely be black)

When belt and pulley are fully seated tighten set screw on pulley making sure set screw is aligned with flat on motor shaft.

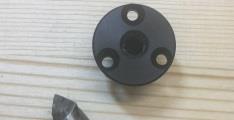
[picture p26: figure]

Countersink the 3 holes in POM nut (supplied with linear motor) .

Install POM nut into the J5 carrier. secure with (3) M3x10 flat head screws.

Note: If additional belt tension is required you can place shims between bracket and aluminum. In this example 4mm nuts are placed between bracket to provide tension.

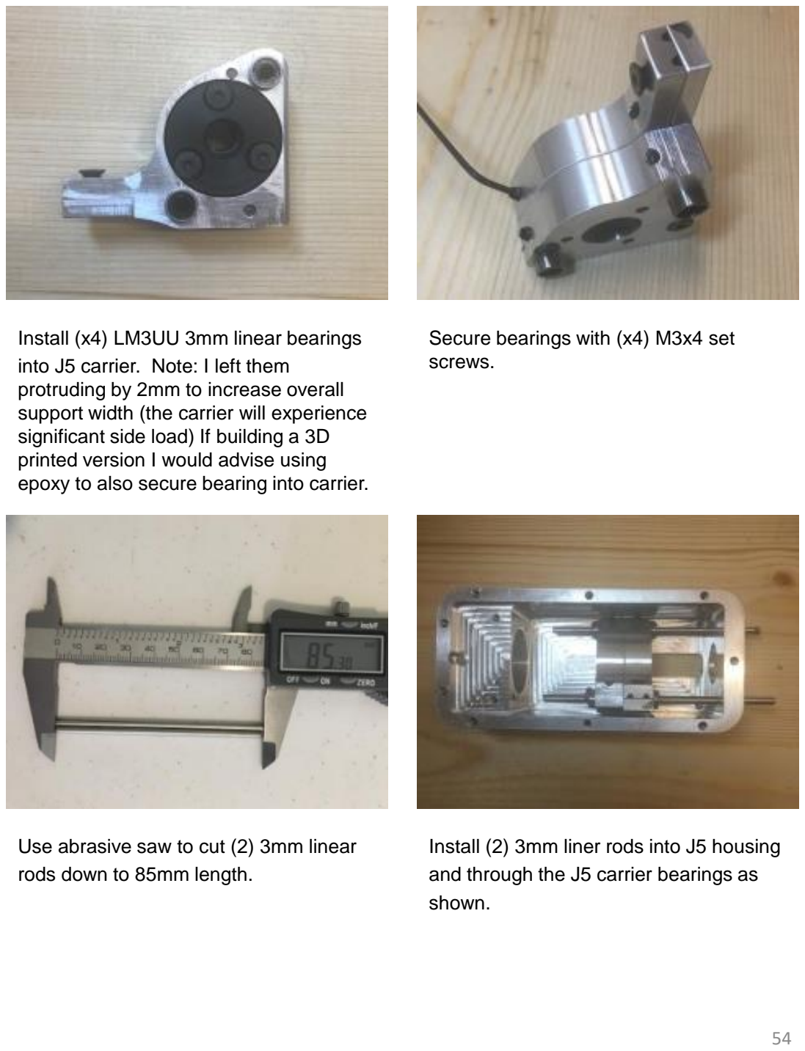
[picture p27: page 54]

Install (x4) LM3UU 3mm linear bearings into J5 carrier. Note: I left them protruding by 2mm to increase overall support width (the carrier will experience significant side load) If building a 3D printed version I would advise using epoxy to also secure bearing into carrier.

Secure bearings with (x4) M3x4 set screws.

Use abrasive saw to cut (2) 3mm linear rods down to 85mm length.

Install (2) 3mm liner rods into J5 housing and through the J5 carrier bearings as shown.

# NOTE ON 3mm ROD DIAMETER

## The diameter of the 3mm rod can vary slightly depending on suppliers. Measure you rods and make sure they are approx. 2.98mm

in diameter and that the 3mm bearings slide on to them easily.

DO NOT FORCE BEARINGS ONTO ROD If you find your rods are slightly larger – approx. 3.04mm this is easily fixed using a drill press, sand paper and scotch-brite. Chuck rod into drill and then evenly polish with 500 or larger grit paper. Check diameter carefully along entire length of shaft then polish thoroughly with scotch-brite. This process only takes a few minutes but its important that the rods are not tight or forced into bearings. The rods should measure approx. 2.98mm

Temporarily install M4x20 cap screw fully threaded into hole as shown (this will prevent 3mm rod from going too deep and blocking hole) then finish sliding 3mm rods into place.

Secure both 3mm rods using (x2) M3x6 set screws – one from the top and one from the bottom. Then remove the M4 cap screw. (Don’t forget to apply grease to 3mm rods and bearings)

Install J5 idler tension block and secure with (2) M3x8 socket head cap screws.

Install HK1612 bearing over the J5 bearing post as shown.

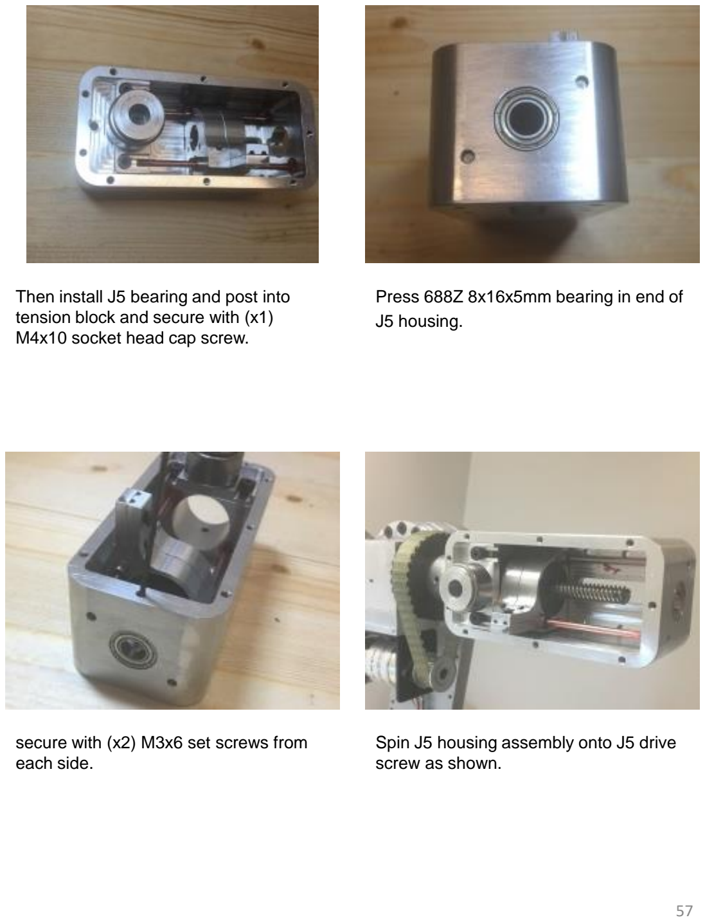
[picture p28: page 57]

Then install J5 bearing and post into tension block and secure with (x1) M4x10 socket head cap screw.

Press 688Z 8x16x5mm bearing in end of J5 housing.

secure with (x2) M3x6 set screws from each side.

Spin J5 housing assembly onto J5 drive screw as shown.

Slide J5 housing assembly forward onto J4 main tube.

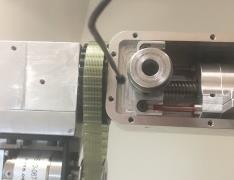
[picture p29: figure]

Install M3x6 set screw and secure J5 housing into tube.

Secure limit switch to J3 turret housing using (x2) M3x14 socket head cap screws.

Press #30203 taper roller bearing race into J5 main bearing support arm.

Secure J6 main bearing arm to J5 housing using (x6) M4x18 flat head screws.

Install J5 limit switch into slot on J6 bearing support arm as shown.

Manually rotate the screw shaft on the J5 motor until the J5 belt carrier is all the way to the end of its stroke as shown.

With carrier at the end of its stroke carefully adjust limit switch so that switch wheel contacts carrier clicks when carrier is forward.

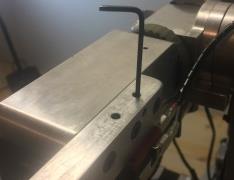
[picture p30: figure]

Install and snug (x2) M4x10 set screws to secure switch in place-be careful not to overtighten (do not damage switch). Rotate J5 motor shaft forward back to make sure limit switch clicks when carrier is in the forward position and adjust switch position as necessary.

Install #30203 taper bearing onto J6 housing side post.

Note: If building 3D printed robot Use epoxy to secure J6 drive post to J6 housing as they are printed in 2 pieces.

Install (x1) .126” thick bearing washer into J6 bearing cap.

Install (1) 1” ID needle bearing into J6 bearing cap.

Install (1) .032” bearing washer into J6 bearing cap on top of bearings.

Install J6 motor bearing assembly into bearing support arm with J6 cap assembly on opposite side and secure with (x1) M6x14 socket head cap screw.

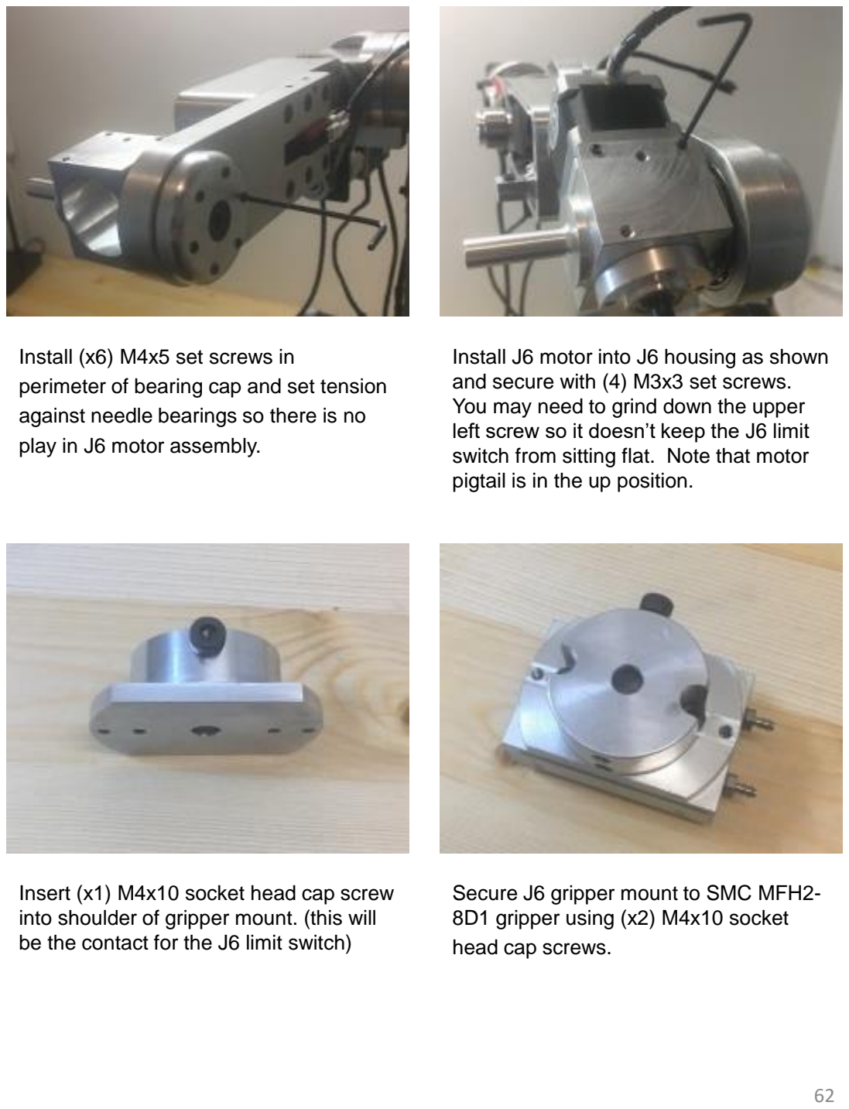
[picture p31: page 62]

Install (x6) M4x5 set screws in perimeter of bearing cap and set tension against needle bearings so there is no play in J6 motor assembly.

Install J6 motor into J6 housing as shown and secure with (4) M3x3 set screws. You may need to grind down the upper left screw so it doesn’t keep the J6 limit switch from sitting flat. Note that motor pigtail is in the up position.

Insert (x1) M4x10 socket head cap screw into shoulder of gripper mount. (this will be the contact for the J6 limit switch)

Secure J6 gripper mount to SMC MFH2-8D1 gripper using (x2) M4x10 socket head cap screws.

Install gripper mount over J6 motor shaft and secure with (x2) M4x10 set screws.

Install plastic J5 side cover and Install (1) XL15 tooth –8mm bore drive sprocket on J6 spindle shaft as shown but do not tighten set screws yet.

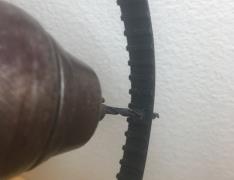
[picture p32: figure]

Use 3mm drill to create small hole in center of 150XL037 belt,

Adjust J5 idler tension block so that belt just barely too tight to fit and tighten mounting screws.

Belt should be just barely too tight so that you cant slip it over the idler bearing.

Note: when using 3D printed components you may not be able to get the belt this tight.

Loosed bearing post mounting screw so that post tips back and belt can now slide onto bearing. Now tighten post mounting screw – this should now result in a very tight belt adjustment.

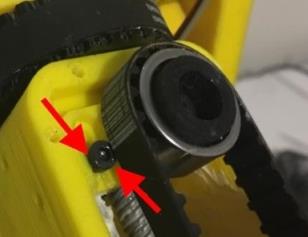
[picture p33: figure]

When using 3D printed components the M4 screws do not have the holding force to keep tension on the belt under load.
Place a small drop of super glue around the heads of the M4 screws securing the head of the screw to the tension block. (if disassembled or tension needs to be reset bond will need to be broken and a new tension block installed)

Install (x1) M3x8 set screw through belt and J5 carrier clamp as shown and tighten to clamp belt to carrier.

Rotate J5 motor shaft until belt carrier is to the top of its stroke and you can feel the J5 limit switch click or make contact. Use angle gauge and rotate J6 housing until housing is at 105°

Once J5 limit switch is clicked and housing is at 105° tighten the pulley set screws as shown.

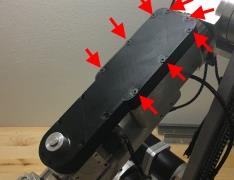
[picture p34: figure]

Install J5 side spacers and cover cap as shown. Secure to J5 housing with (8) M3x25 flat head screws.(these go through the cap, spacer and side plate and then thread into the J5 housing)

Secure the cover & spacer to the side plate on the front using (6) M3x20 flat head screws. (these thread into shallow threads on the plastic side plate)

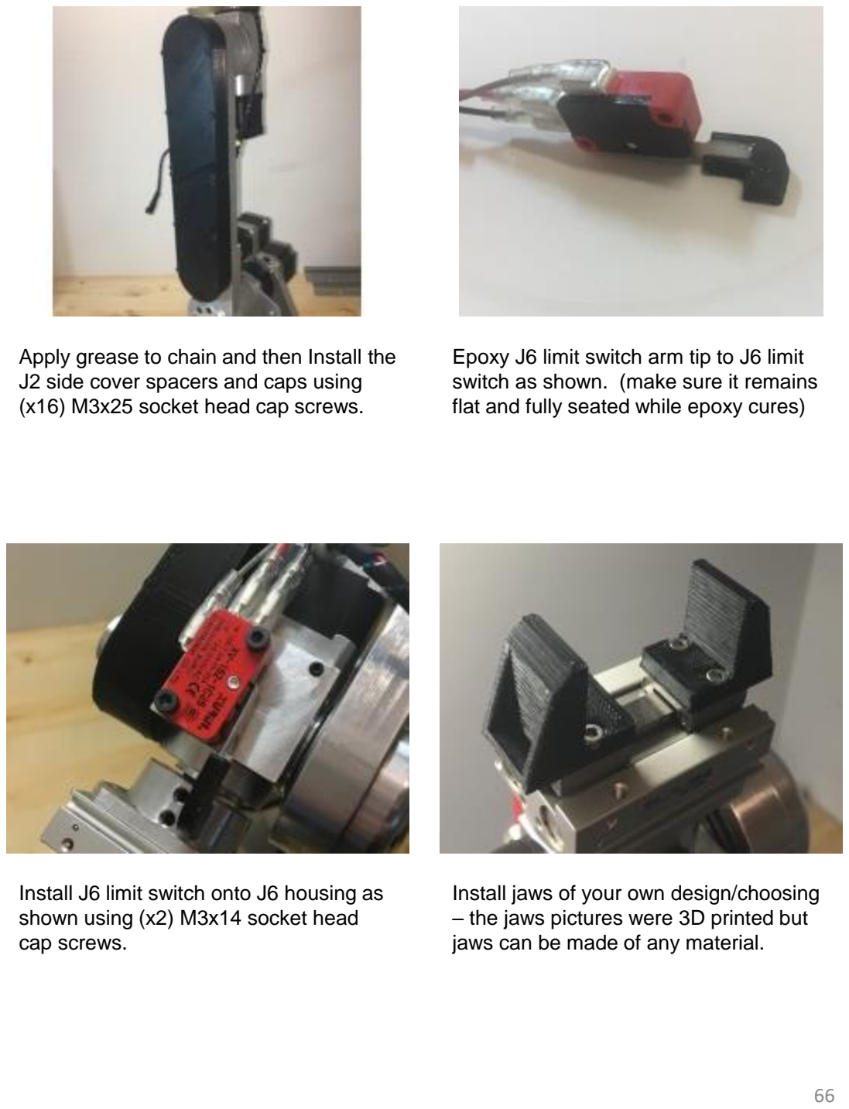
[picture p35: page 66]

Apply grease to chain and then Install the J2 side cover spacers and caps using (x16) M3x25 socket head cap screws.

Epoxy J6 limit switch arm tip to J6 limit switch as shown. (make sure it remains flat and fully seated while epoxy cures)

Install J6 limit switch onto J6 housing as shown using (x2) M3x14 socket head cap screws.

Install jaws of your own design/choosing – the jaws pictures were 3D printed but jaws can be made of any material.

If you are building a 3D printed version use epoxy to attach (x6) auxiliary support braces evenly spaced around J1 turret for added rigidity.

If you are building a 3D printed version use epoxy to attach J2 auxiliary support brace as shown for added rigidity.

Mechanical assembly of the robot is now complete. Please review the wiring harness, electrical enclosure and startup manuals to complete robot build.

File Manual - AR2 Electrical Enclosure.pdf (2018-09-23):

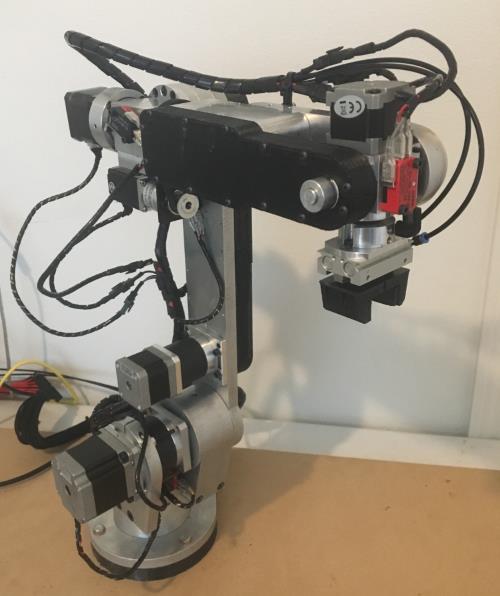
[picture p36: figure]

# Model AR2 Electrical Enclosure

# ELECTRICAL PANEL ASSEMBLY

# BILL OF MATERIALS

## www.omc-stepperonline.com (https://www.omc-stepperonline.com/?tracking=59c1139e8987b)

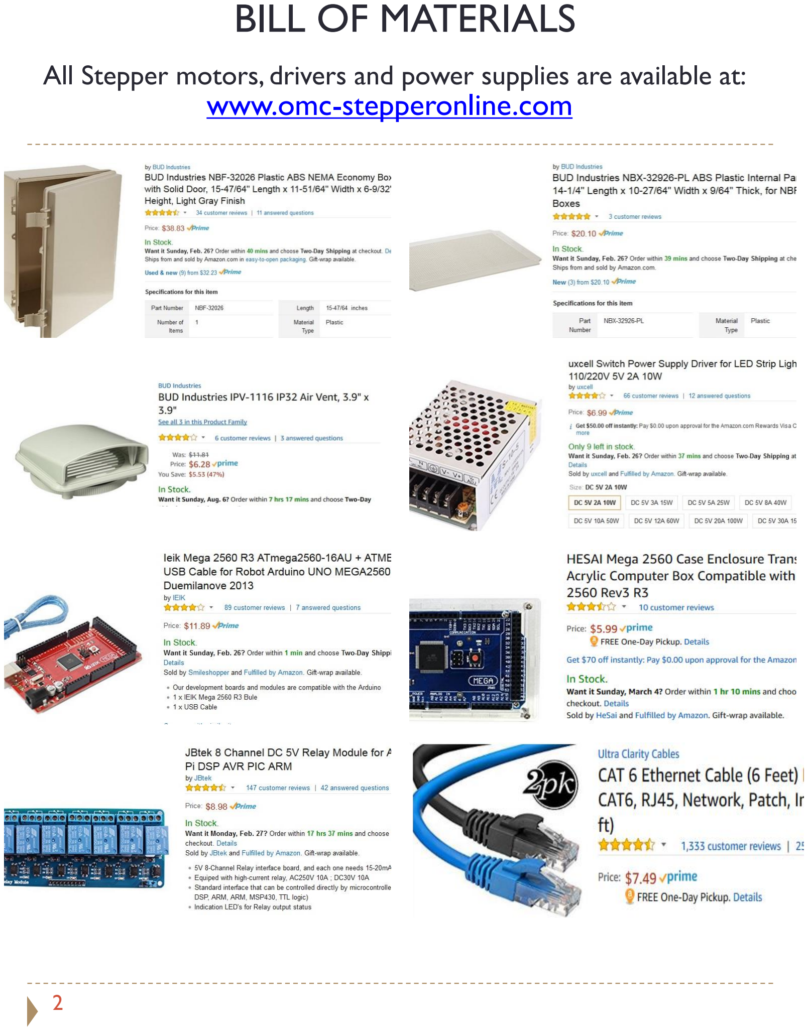
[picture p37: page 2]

2

## All Stepper motors, drivers and power supplies are available at:

## BILL OF MATERIALS CONTINUED

3

NOTE: This terminal block shield is optional – it makes some connections easier.

## BILL OF MATERIALS CONTINUED

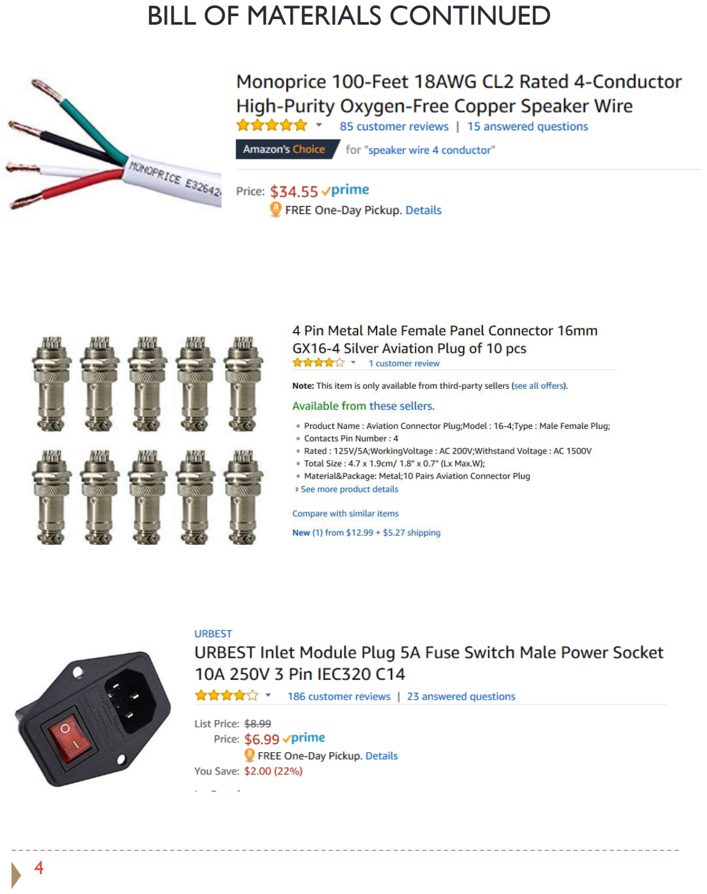
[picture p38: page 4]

4

## BILL OF MATERIALS CONTINUED

5

## www.omc-stepperonline.com (https://www.omc-stepperonline.com/?tracking=59c1139e8987b)

24 volt power supply | DM542T drivers for axis 1,2,3,5,6 and travel track.

DM320T drivers for axis 4

# ASSEMBLY

6

Trace bolt pattern from
bottom of 24vdc power
supply onto a sheet of paper and transfer bolt pattern to bottom of enclosure as
shown. Drill 5mm holes
where marked.

Install backplane into bottom of enclosure using the
supplied screws.

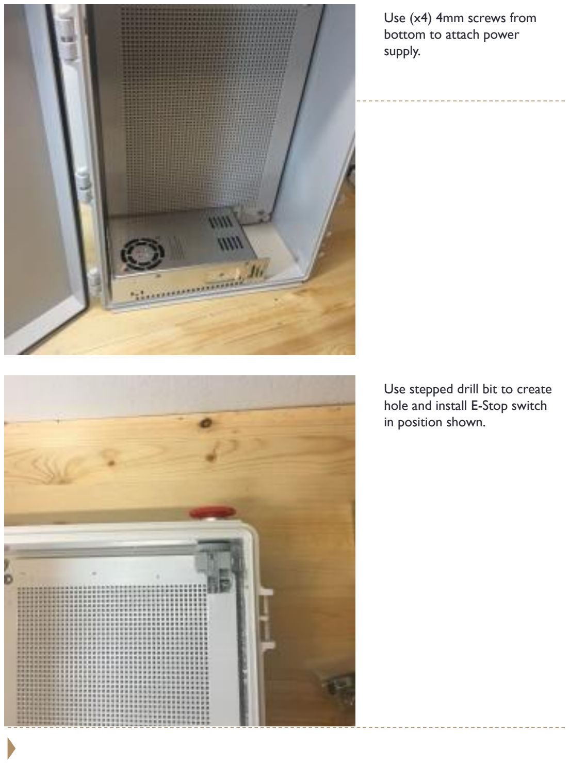
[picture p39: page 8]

Use stepped drill bit to create hole and install E-Stop switch in position shown.

Use (x4) 4mm screws from
bottom to attach power
supply.

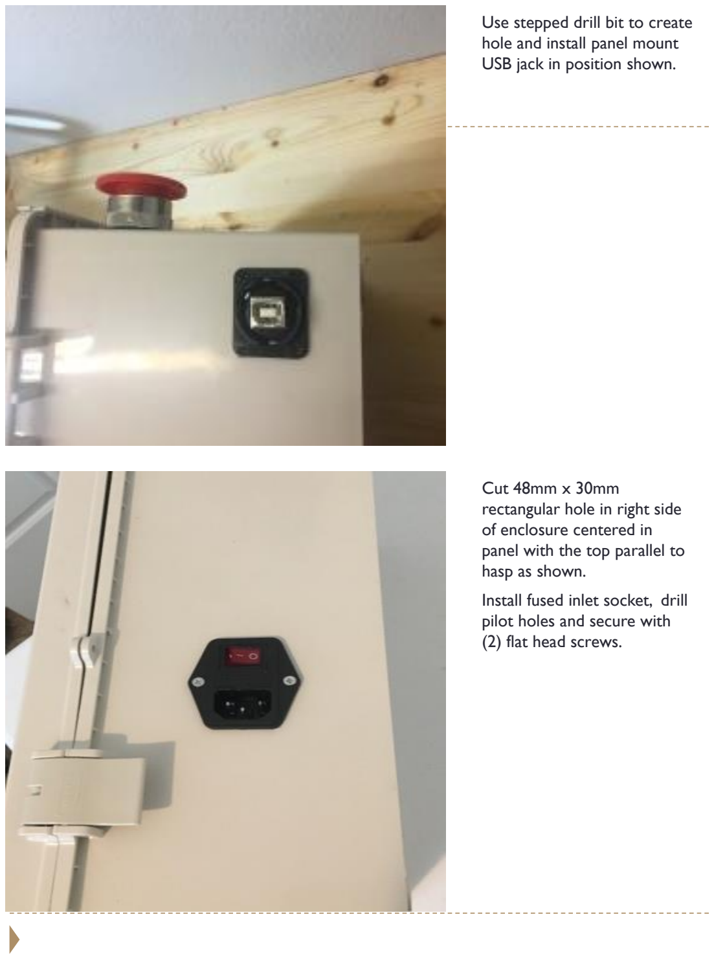
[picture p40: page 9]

Cut 48mm x 30mm
rectangular hole in right side of enclosure centered in
panel with the top parallel to hasp as shown.

Install fused inlet socket, drill pilot holes and secure with
(2) flat head screws.

Use stepped drill bit to create hole and install panel mount USB jack in position shown.

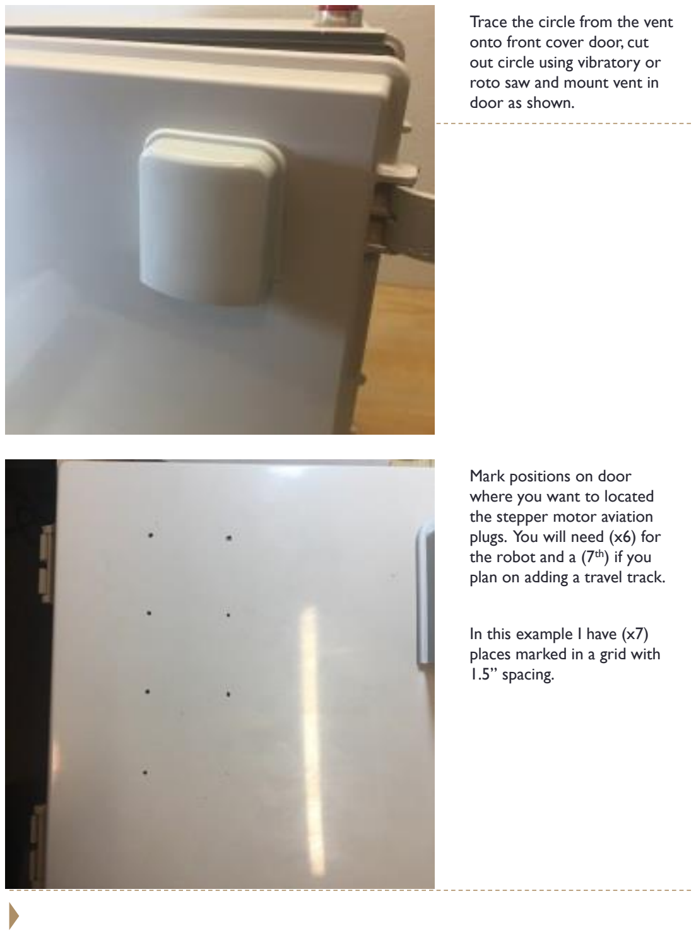
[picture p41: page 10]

Mark positions on door
where you want to located
the stepper motor aviation plugs. You will need (x6) for the robot and a (7th) if you plan on adding a travel track.

In this example I have (x7) places marked in a grid with 1.5” spacing.

Trace the circle from the vent onto front cover door, cut out circle using vibratory or roto saw and mount vent in door as shown.

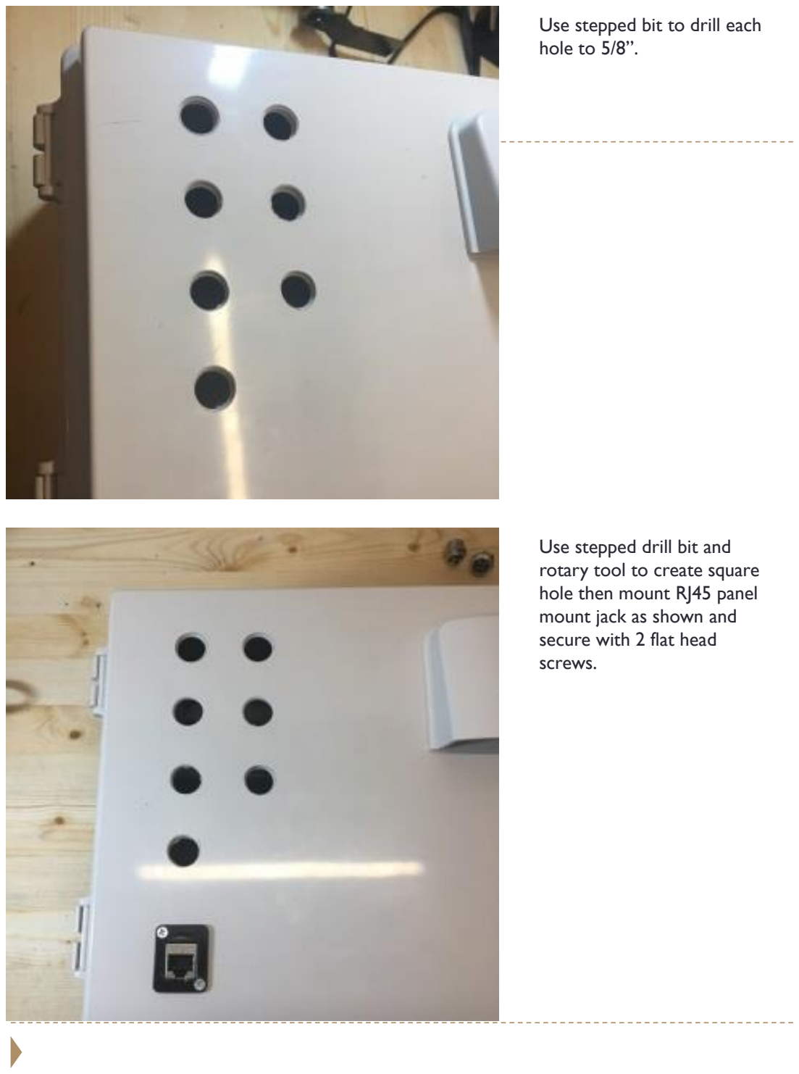
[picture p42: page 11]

Use stepped drill bit and
rotary tool to create square hole then mount RJ45 panel mount jack as shown and
secure with 2 flat head
screws.

Use stepped bit to drill each hole to 5/8”.

Mount length of DIN rail in position shown.

Mount stepper drivers as
shown. I mounted the smaller DM320T up top to the right of backplane screw and the remaining DM542T drivers
below that. If you plan on using a travel track install a 7th driver at the bottom.

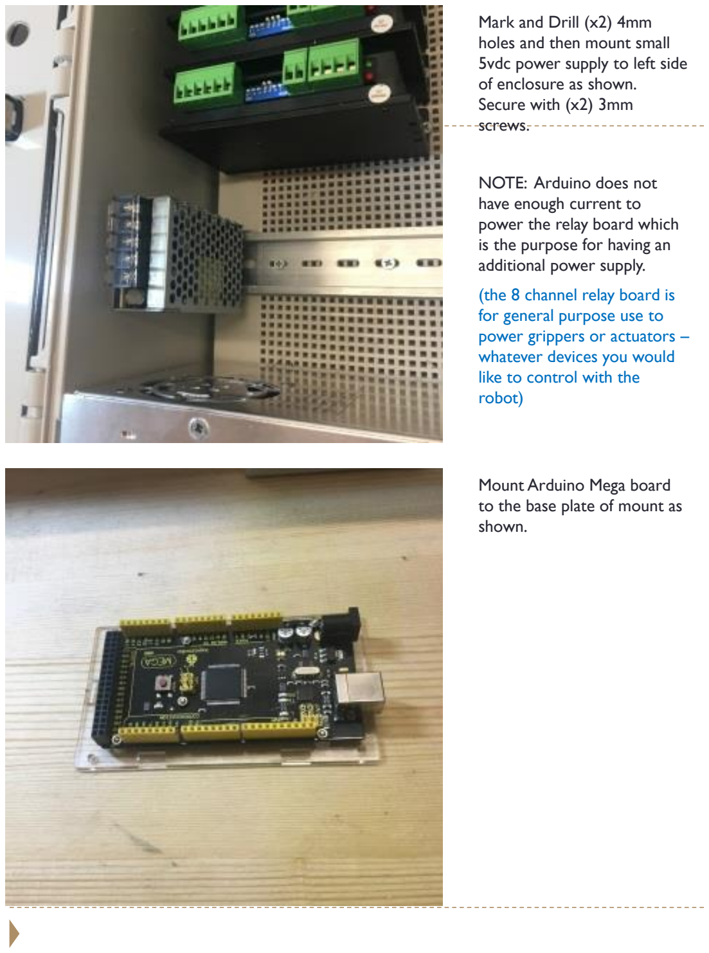
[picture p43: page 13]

Mount Arduino Mega board
to the base plate of mount as shown.

Mark and Drill (x2) 4mm
holes and then mount small 5vdc power supply to left side of enclosure as shown.
Secure with (x2) 3mm
screws.

NOTE: Arduino does not
have enough current to
power the relay board which is the purpose for having an additional power supply.

(the 8 channel relay board is for general purpose use to power grippers or actuators – whatever devices you would like to control with the
robot)

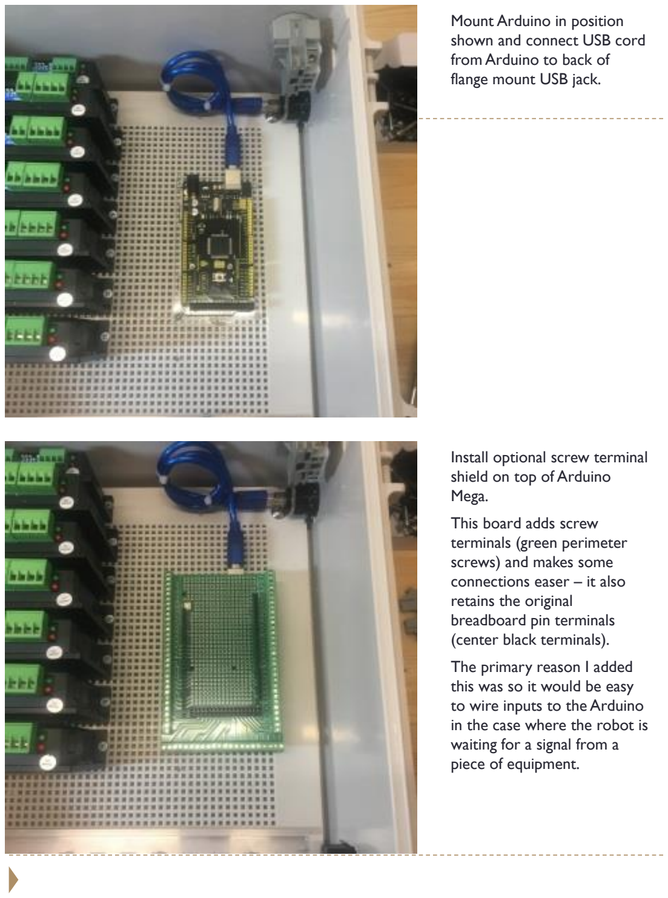
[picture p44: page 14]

Install optional screw terminal shield on top of Arduino
Mega.

This board adds screw
terminals (green perimeter screws) and makes some
connections easer – it also retains the original
breadboard pin terminals
(center black terminals).

The primary reason I added this was so it would be easy to wire inputs to the Arduino in the case where the robot is waiting for a signal from a piece of equipment.

Mount Arduino in position
shown and connect USB cord from Arduino to back of
flange mount USB jack.

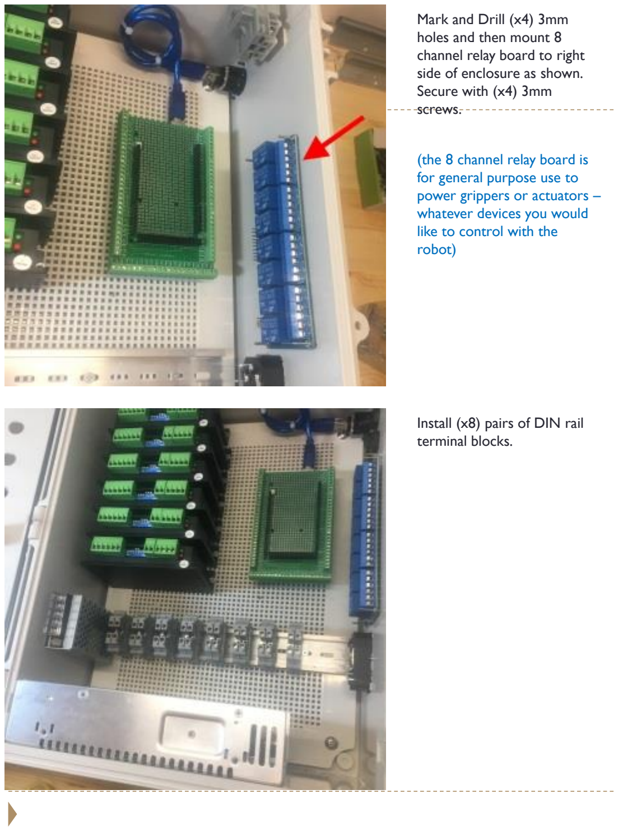
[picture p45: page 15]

Install (x8) pairs of DIN rail terminal blocks.

Mark and Drill (x4) 3mm
holes and then mount 8
channel relay board to right side of enclosure as shown. Secure with (x4) 3mm
screws.

(the 8 channel relay board is for general purpose use to power grippers or actuators – whatever devices you would like to control with the
robot)

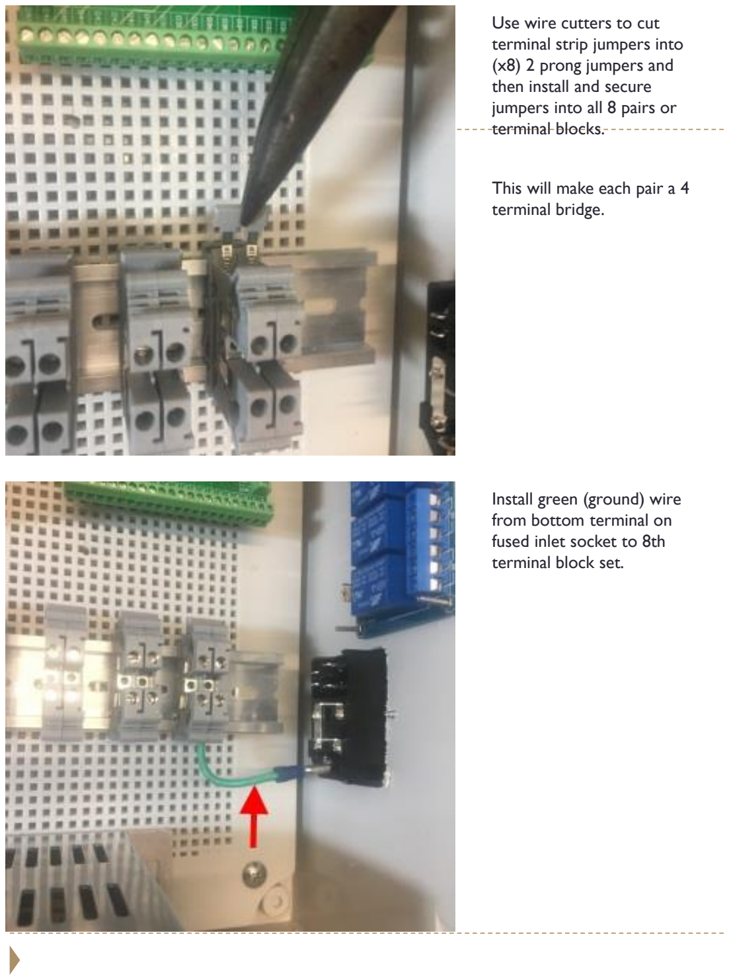
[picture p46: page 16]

Install green (ground) wire from bottom terminal on
fused inlet socket to 8th
terminal block set.

Use wire cutters to cut
terminal strip jumpers into (x8) 2 prong jumpers and
then install and secure
jumpers into all 8 pairs or terminal blocks.

This will make each pair a 4 terminal bridge.

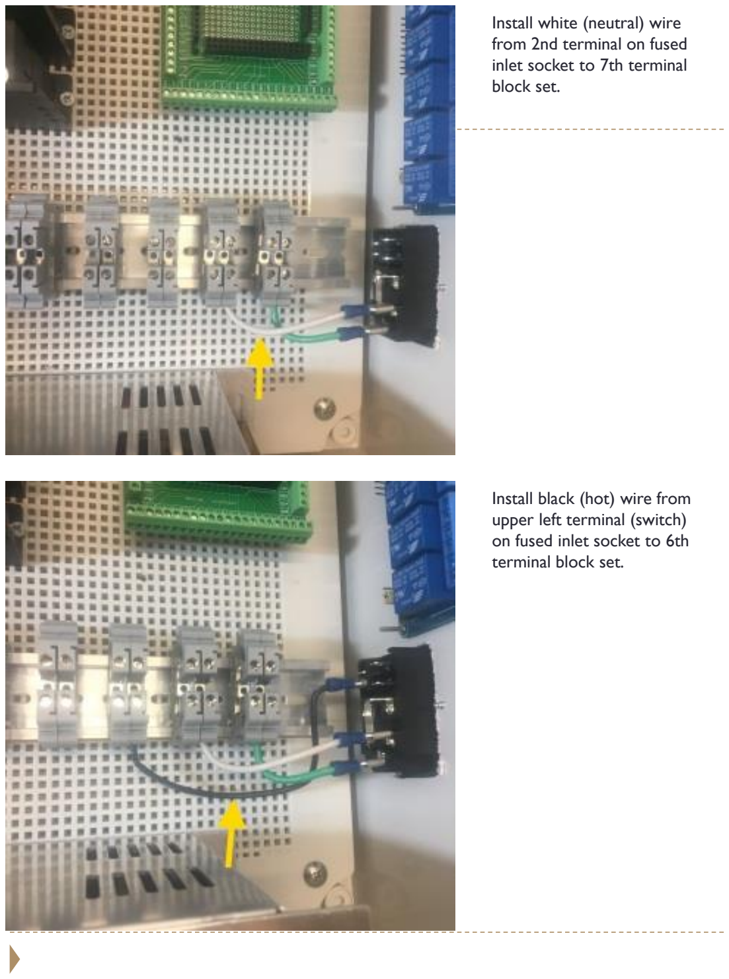
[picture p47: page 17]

Install black (hot) wire from upper left terminal (switch) on fused inlet socket to 6th terminal block set.

Install white (neutral) wire from 2nd terminal on fused inlet socket to 7th terminal block set.

Install Ground wire from 8th terminal block to ground
terminal on 24vdc power
supply.

Install Neutral wire from 7

th
terminal block to Neutral
terminal on 24vdc power
supply.

Install Hot/Line wire from 6th terminal block to Line
terminal on 24vdc power
supply.

Install black (hot) jumper wire from 3

rd terminal to upper
right terminal (switch) on fused inlet socket.

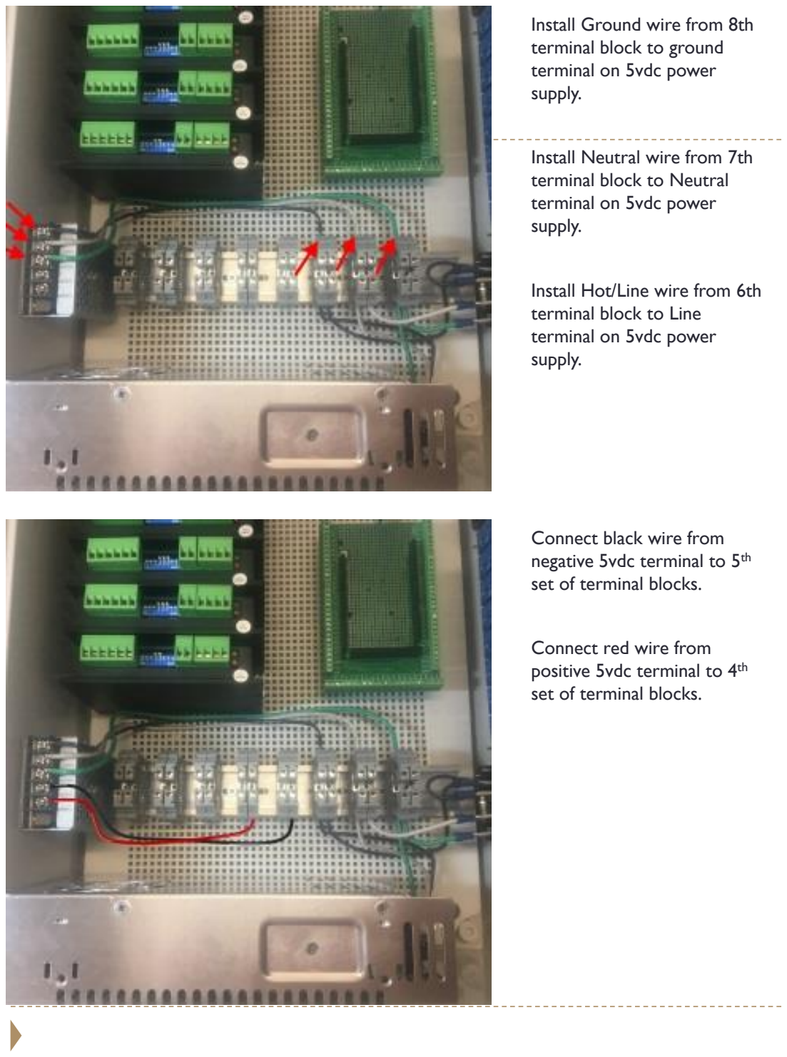
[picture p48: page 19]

Connect black wire from
negative 5vdc terminal to 5th set of terminal blocks.

Connect red wire from
positive 5vdc terminal to 4

th
set of terminal blocks.

Install Ground wire from 8th terminal block to ground
terminal on 5vdc power
supply.

Install Neutral wire from 7th terminal block to Neutral
terminal on 5vdc power
supply.

Install Hot/Line wire from 6th terminal block to Line
terminal on 5vdc power
supply.

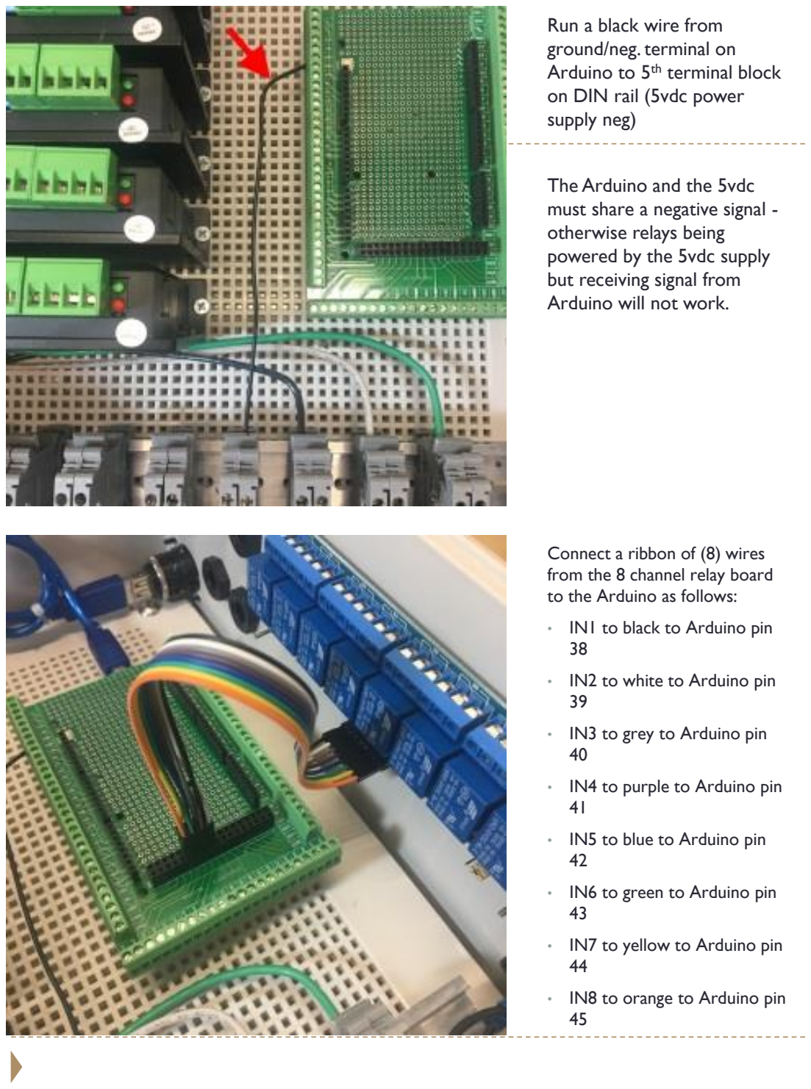
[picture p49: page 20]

Connect a ribbon of (8) wires from the 8 channel relay board to the Arduino as follows:

- IN1 to black to Arduino pin 38
- IN2 to white to Arduino pin 39
- IN3 to grey to Arduino pin 40
- IN4 to purple to Arduino pin 41
- IN5 to blue to Arduino pin 42
- IN6 to green to Arduino pin 43
- IN7 to yellow to Arduino pin 44
- IN8 to orange to Arduino pin 45

Run a black wire from
ground/neg. terminal on
Arduino to 5th terminal block on DIN rail (5vdc power
supply neg)

The Arduino and the 5vdc
must share a negative signal -otherwise relays being
powered by the 5vdc supply but receiving signal from
Arduino will not work.

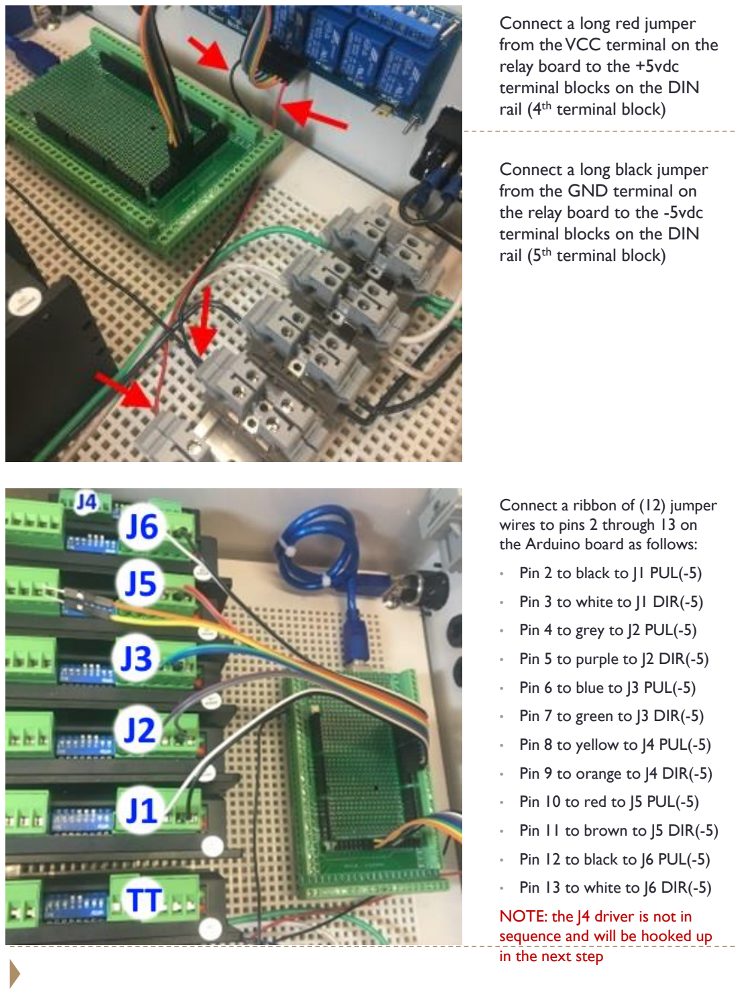
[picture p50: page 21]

Connect a ribbon of (12) jumper wires to pins 2 through 13 on the Arduino board as follows:

- Pin 2 to black to J1 PUL(-5)
- Pin 3 to white to J1 DIR(-5)
- Pin 4 to grey to J2 PUL(-5)
- Pin 5 to purple to J2 DIR(-5)
- Pin 6 to blue to J3 PUL(-5)
- Pin 7 to green to J3 DIR(-5)
- Pin 8 to yellow to J4 PUL(-5)
- Pin 9 to orange to J4 DIR(-5)
- Pin 10 to red to J5 PUL(-5)
- Pin 11 to brown to J5 DIR(-5)
- Pin 12 to black to J6 PUL(-5)
- Pin 13 to white to J6 DIR(-5)

NOTE: the J4 driver is not in sequence and will be hooked up in the next step

Connect a long red jumper
from the VCC terminal on the relay board to the +5vdc
terminal blocks on the DIN rail (4th terminal block)

Connect a long black jumper from the GND terminal on
the relay board to the -5vdc terminal blocks on the DIN rail (5th terminal block)

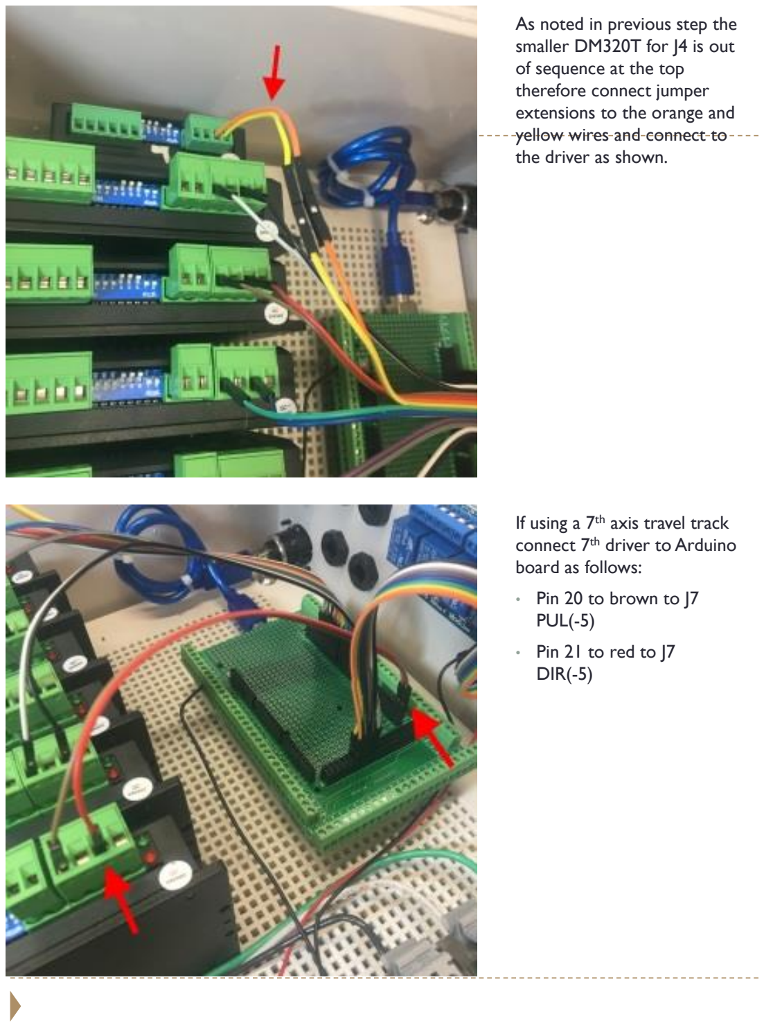
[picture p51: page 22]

If using a 7th axis travel track connect 7th driver to Arduino board as follows:

- Pin 20 to brown to J7
PUL(-5)
- Pin 21 to red to J7
DIR(-5)

As noted in previous step the smaller DM320T for J4 is out of sequence at the top
therefore connect jumper
extensions to the orange and yellow wires and connect to the driver as shown.


The next step is to run 5vdc to all the (+5v) terminals across all of the stepper drivers. The drivers are NPN or negative switching which means the step and direction pulses will be made by the negative wire and the positive is high or on all the time on all the (+5v) terminals. Each driver has (2) positive terminals that require a constant +5v signal:

- PUL+(+5)
- DIR+(+5)

Run a long jumper from the 4th terminal block to the bottom stepper drivers DIR+(+5) and jumper that over to the PUL+(+5), then jumper to the next driver and across its (2) (+5) terminals and continue up and across all drivers – you will need a total of (12) short jumper wires.

NOTE: when you get to the top DM320T driver it only as one (+5) terminal which is labeled “Opto”.

(Also refer to the full wiring diagram at the end of this manual )

- For the next step you will need to jumper +5vdc
across all +driver terminals. Use 12 short red jumpers
and one long red jumper -
twist ends together end to end so you have a chain of jumpers. Test continuity
across all jumpers before
installing.

(Also refer to the full wiring diagram at the end of this manual )


Run brown wire from +24vdc terminal power supply up to one terminal on E-Stop
switch then run brown wire from other terminal on E-Stop switch back down to the 2

nd terminal block.

Run blue wire from -24vdc
terminal on power supply to the 3rd terminal block.


Jumper -24vdc from terminal block #3 across all drivers

-voltage terminals using blue wire.

Jumper +24vdc from terminal block #2 across all drivers

+voltage terminals using
brown wire.

Photo shows brown wire
from +24vdc going up to
estop and coming back down and tied into terminal block 7.


Tin the wire ends with solder as shown. Also pre-apply
solder to the solder
connection joints on the
aviation plugs.

Cut (x6) 20” long lengths of 4 strand cable.

Cut a 7th if installing driver for a 7th axis travel track.


Repeat this for all
motor/driver wires.

Solder wires as shown to the rear of the aviation plug.

This diagram shows the which termals to solder which wire color. Note: this is showing the connector from the
backside where wires
connect.


Mark each wire for which
driver it will go to. Facing the enclosure door J1 is top left.

Install all driver/motor wires and Ethernet cable as shown.

Connect each wire to its
corresponding driver.

BLACK = A+

GREEN = A-

RED = B+

WHITE = B-

Install adhesive cable tie anchor and loom cables as
shown.


Connect RJ45 wires as
follows:
- RJ45 white/or stripe to
arduino pin 14
- RJ45 or/white stripe to
arduino pin 15
- RJ45 white/gr stripe to
arduino pin 16
- RJ45 blue/white stripe to arduino pin 17
- RJ45 white/blue stripe to arduino pin 18
- RJ45 green/white stripe to arduino pin 19

Route Ethernet wire as
shown. (You will need to cut and strip wires from board connection end of cable).


## ENABLE CIRCUIT

NOTE: The enable circuit wiring was not shown in this manual. The wiring for the enable circuit is shown in the electrical schematic. The enable circuit is used to disable all drivers – this could be used in a situation where you have a fence circuit that you want to disable the robot while a gate is open or a condition is not made. In this case you would jumper +5vdc to all +ENA terminals on drivers and then jumper all –ENA terminals together and connect to terminal bock #1. You could then connect any -5vdc grounding fence circuit to a terminal on terminal block #1 and all drivers will be disabled while fence is open or ground is made.

- RJ45 brown/wh stripe to
arduino +5v
- RJ45 white/brown stripe to arduino GND

THESE SETTINGS ARE USED FOR THE FOLLOWING SERIES MOTORS:

- J1 - 17HS15-1684S-HG20 | 1/1 STEPS | 1.46 AMP
- J2 - 23HS22-2804S-HG50 | 1/2 STEPS | 2.37 AMP
- J3 - 17HS15-1684S-HG50 | 1/2 STEPS | 1.46 AMP
- J4 - 11HS20-06742-PG14 | 1/2 STEPS | .5 AMP
- J5 - 17LS19-1684E-200G | 1/4 STEPS | 1.46 AMP
- J6 - 14HS13-0804S-PG19 | 1/2 STEPS | 1 AMP
- J7 – Nema 17 48mm body | 1/2 STEPS | 1.46 AMP

J1 – (DM542T):
SW1 = OFF SW2 = ON | SW3 = ON | SW4 = ON
SW5 = ON | SW6 = ON | SW7 = ON | SW8 = ON

J2 – (DM542T):
SW1 = OFF SW2 = OFF SW3 = ON | SW4 = ON
SW5 = OFF SW6 = ON | SW7 = ON | SW8 = ON

J3 – (DM542T):
SW1 = OFF SW2 = ON | SW3 = ON | SW4 = ON
SW5 = OFF SW6 = ON | SW7 = ON | SW8 = ON

J4 – (DM320T):
SW1 = ON | SW2 = OFF SW3 = ON
SW4 = ON SW5 = ON | SW6 = ON

J5 – (DM542T):
SW1 = OFF SW2 = ON | SW3 = ON | SW4 = ON
SW5 = ON | SW6 = OFF SW7 = ON | SW8 = ON

J6 – (DM542T):
SW1 = ON | SW2 = ON | SW3 = ON | SW4 = ON
SW5 = OFF SW6 = ON | SW7 = ON | SW8 = ON

NOTE: If using a 7th joint travel track (nema 17) use the same setting as J1.

## ROBOT GRIPPER

33

### You can use any type of gripper you like including electric servo grippers or pneumatic

grippers.

### If using a servo gripper you would connect your servo to one of the Arduino analog pins 0 through 7 and then use the “Servo” position command button to control your

gripper.

### If using a pneumatic gripper you would connect a 24vdc solenoid valve to one of the relay outputs (Arduino outputs 38 through 45) and then use the “Set Output On” and

“Set Output Off” commands to program relays to control your gripper.

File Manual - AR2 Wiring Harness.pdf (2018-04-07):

# Model AR2 Wiring Harness

# WIRING HARNESS ASSEMBLY

# BILL OF MATERIALS

## www.omc-stepperonline.com (https://www.omc-stepperonline.com/?tracking=59c1139e8987b)


2

## All Stepper motors, drivers and power supplies are available at:

3

4

5

## (you will need 2 packs of 10 aviation plugs)

6

(Make sure you buy high quality non roller switch for J6 – note the rivet hinge pin)

7

## You will need 1 limit switch tip

For J6, this part must be 3D printed.

## The print file can be found on The project page with all the other

3D print files.

# SECTION 1

# FEMALE 4 PIN JST CONNECTOR FOR MOTOR END OF WIRING HARNESS

8

NOTE THAT THE GAP ON THE PIN INSULATION WINGS IS TYPICALLY TOO WIDE OR TOO OPEN.

BEND AND BREAK OFF FEMALE PIN FROM STRIP.

THE GAP SHOULD NOW LOOK LIKE THIS.

USE NEEDLE NOSE PLIERS TO CLOSE THE GAP AS SHOWN


STRIP END LEAVING APPROX 3mm OF WIRE EXPOSED ON ALL 4 WIRES.

PLACE END OF RIBBON WIRE IN SELF ADJUSTING WIRE STRIPPERS AS SHOWN.

NOTE THE LIP OR STEP IN THE UPPER JAW OF THE CRIMPING TOOL.

USE CUTTERS OR RAZOR KNIFE TO SEPARATE WIRES.

CLOSE THE CRIMPER SLOWLY INTIL THE RATCHET MECHANISM CLICKS 3 TIMES BUT DO NOT FULLY CLAMP. IT SHOULD LOOK LIKE THIS.

WITH CRIMPING TOOL UPSIDE DOWN IN YOUR LEFT HAND PLACE THE FEMALE PIN INTO THE JAW WITH YOUR RIGHT HAND AS SHOWN. THE WINGS
SHOULD BE UP AGAINST THE STEP SHOWN IN THE PREVIOUS STEP..


THIS PICTURE SHOWS WHERE THE WIRE SHOULD BE SITTING INSIDE THE PIN.

NOTE THE JACKET IS JUST PAST THE LARGE WINGS AND THE WIRE ITESELF IS INSIDE THE SMALLER SET OF WINGS.

IT WILL TAKE PRACTICE TO GET A FEEL FOR HOW TO INSERT THE WIRE INTO THE CRIMPER TO GET THIS ALIGNMENT.

FLIP THE CRIMPER BACK RIGHT SIDE UP AND HOLD WITH YOUR RIGHT HAND, THEN STARTING WITH THE BLUE WIRE AS SHOWN – INSERT THE WIRE INTO THE CRIMPER AND PIN.

THIS PICTURE SHOWS HOW IT SHOULD LOOK AFTER BEING CRIMPED.

NOTE THE JACKET IS FULLY CLAMPED BY THE LARGE WINGS BUT THE JACKET STOPS RIGHT AT THE SMALLER WINGS AND THE SMALLER WINGS HAVE CLAMPED ONLY THE METAL WIRE.

I SUGGEST PRACTICING THIS SEVERAL TIMES TO GET THE HANG OF IT BEFORE TRYING TO MAKE YOUR WIRING HARNESS.

WITH THE WIRE AT THE CORRECT DEPTH COMPETEY CLAMP THE CRIMPER.


THIS PICTURE ALSO SHOWS AN INCORRECTLY CRIMPED
CONNECTOR.

NOTE THE WIRE WAS INSERTED TOO FAR AND THE JACKET IS
CLAMPED BY BOTH THE LARGE
AND SMALL WINGS.

THIS IS NOT ACCEPTABLE – IF IT LOOKS LIKE THIS YOU NEED TO RE-DO IT..

THIS PICTURE SHOWS AN
INCORRECTLY CRIMPED
CONNECTOR.

NOTE THE JACKET IS NOT FULLY INSIDE OR CLAMPED BY THE
WINGS.

THIS IS NOT ACCEPTABLE – IF IT LOOKS LIKE THIS YOU NEED TO RE-DO IT.

CUT A LENGTH OF HEAT SHRINK TUBING APPROX 25mm LONG AND RUN WIRES THROUGH IT AS SHOWN.

ONCE YOU HAVE MASTERED CRIMPING CONTINUE CRIMPING A PIN ON ALL 4 WIRES AS SHOWN.

PINCH EACH CONNECTOR IN YOUR FINGERS AND TUG ON IT TO MAKE SURE IT DOESN’T COME OFF EASILY. IF IT COMES OFF IT OBVIOSLY NEEDS TO BE REDONE AND WASN’T FULLY CRIMPED.

START TO FEED WIRES INTO FEMALE HOUSING AS SHOWN.

USE A RAZOR BLADE TO MAKE SURE THE TANGS ON EACH PIN ARE POINTED OUT.

SOMETIMES THEY GET FLATTENED AND WILL NOT LATCH INTO THE PLASTIC HOUSING.


APPLY BLACK SILICONE AROUND THE BASE OF THE CONNECTOR ON BOTH SIDES AS SHOWN.

CONTINUE TO FULLY INSERT WIRES INTO HOUSING.

NOTE THE TANGS ARE FULLY INSERTED INTO THE SLOTS AND DO NOT PULL BACK OUT

NOTE WITH THE SLOTS FACING YOU THE BLUE WIRE IS ON TOP, THEN RED, GREEN AND BLACK ON THE BOTTOM. IT IS IMPORTANT THEY ARE INSERTED IN THIS ORDER.

AFTER WORKING SILICONE INTO CONNECTOR SPREAD IT A SHORT WAY DOWN THE WIRES – IT SHOULD LOOK LIKE THE PICTURE.

USE A TOOTHPICK TO WORK SILICONE INTO EACH JACKET ON BOTH SIDES.

USE A HEAT GUN TO SHRINK THE TUBING AS SHOWN.

THIS CONNECTOR IS NOW COMPLETE

SLIDE THE LENGTH OF HEAT SHRINK TUBING OVER THE CONNECTOR AS SHOWN.

# SECTION 2

## FEMALE 3 PIN JST CONNECTOR FOR LIMIT SWITCH END OF WIRING HARNESS

22


INSERT WIRES WITH FEMALE PINS INTO THE 3 PIN FEMALE JST HOUSING AS SHOWN.

NOTE WITH THE SLOTS FACING YOU THE RED WIRE IS ON TOP, THEN GREEN AND BLACK ON THE BOTTOM. IT IS IMPORTANT THEY ARE INSERTED IN THIS ORDER.

REMOVE THE BLUE STRAND FROM THE RIBBON WIRE AS THIS CONNECTOR ONLY REQUIRES 3 WIRES.

CRIMP FEMALE PINS TO THE ENDS OF EACH OF THE WIRES STARTING WITH THE RED WIRE AS SHOWN – REFER TO INSTRUCTIONS IN SECTION 1 FOR CRIMPING DETAILS.

APPLY SILICONE AND HEAT SHRINK TUBING AS OUTLINED IN SECTION 1.

THIS CONNECTOR IS NOW COMPLETE.

# SECTION 3

# MALE 3 PIN JST CONNECTOR LIMIT SWITCH PIGTAILS

25

NOTE THE LIMIT SWITCH FOR AXIS 6 USES A STRAIGH ARM LIMIT SWITCH WITH THE J6 LIMIT SWITCH TIP ATTACHED.

LIGHTLY SAND END OF LIMIT SWICH ARM ON BOTH SIDES AND THEN USE EPOXY TO SECURE J6 LIMIT SWITCH TIP TO ARM OF SWITCH.

.STL PRINT FILE FOR THIS TIP CAN BE FOUND ON PROJECT PAGE INCLUDED WITH THE OTHER PRINT FILES FOR THE COMPLETE PRINTED ROBOT.

CONNECT BLACK, RED AND GREY 22 AWG QUICK DISCONNECT WIRES TO EACH LIMIT SWITCHES FOR ALL 6 AXIS.

NOTE: J1 THROUGH J5 WILL USE THE ROLLER LIMIT SWICH SHOWN. J6 WILL USE A STRAIGH ARM WITH TIP EXTENSION SHOWN IN THE NEXT STEP.

## Cut quick disconnect wires to length for each switch as shown below

27


INSERT WIRES INTO MALE JST HOUSING AS SHOWN –WITH CLIP FACING FORWARD INSERT RED WIRE ON TOP, GREY IN THE MIDDLE AND BLACK ON THE BOTTOM.

CRIMP JST MALE PINS TO RED, GREY AND BLACK WIRES IN THE EXACT SAME PROCEEDURE OUTLINED IN SECTION 1 FOR ALL 6 LIMIT SWITCHES.

PLACE SILICONE AROUND WIRES AT BASE OF JST HOUSING AND WORK SILICONE INTO REAR OF CONNECTOR IN THE SAME WAY SHOWN IN SECTION 1.

INSERT PINS UNTIL THEY ARE FULLY SEATED AND CLICK INTO THE
HOUSING.


PLACE SHORT LENGTH OF HEAT SHRINK TUBE OVER WIRES AND ONTO JST CONNECTOR AS SHOWN.

WRAP WIRES WITH 4mm SPIRAL WRAP – MAKE SURE SPIRAL WRAP EMBEDS INTO SILICONE BEFORE IT CURES.

AFTER ALL 6 LIMIT SWITCH PIGTAILS ARE COMPLETE USE PAINT PENS TO MARK THE CONNECTORS AS SHOWN ON THE NEXT PAGE

USE HEAT GUN TO SHRINK TUBING AROUND CONNECTOR AND WIRES.

## MARK CONNECTORS AS SHOWN

32

# SECTION 4

# MALE 4 PIN JST CONNECTOR ON MOTOR PIGTAILS

33

## CUT MOTOR WIRES TO THE FOLLOWING LENGTHS


34

SLIDE SHORT LENGTH OF HEAT SHRINK TUBE OVER WIRES.

CRIP MALE JST PINS AS OUTLINED IN SECTION 1TO EACH WIRE ON ALL 6 MOTORS.


INSERT WIRES INTO MALE JST HOUSING AS SHOWN. – MAKE SURE THEY FULLY CLICK INTO PLACE.

MAKE SURE WITH THE CLIP FACING YOU THAT THE BLUE WIRE IS ON THE LEFT, THEN THE RED, GREEN, AND BLACK ON THE RIGHT.

NOTE: THE MOTORS FOR J5 AND J6 HAVE DIFFERENT WIRE COLORS, SEE ELECTRICAL SCHEMATIC FOR CORRECT COLOR ORDER.

WRAP 4mm SPIRAL WRAP AROUND WIRES AND SLIDE UNDER HEAT SHRINK WRAP AS ITS WRAPPED.

J5 motor | J6 motor

FINSIH WRAPPING SPRIRAL WRAP INTIL WRAP IS EMBEDDED INTO SILICONE..

APPLY BLACK SILICONE TO WIRES AND CONNECTOR –WORK SILICONE INTO BACK OF CONNECTOR WITH TOOTH PICK.

USE HEAT GUN TO SHRINK TUBING AS SHOWN.

SLIDE HEAT SHRINK TUBE OVER CONNECTOR AS SHOWN.

APPLY BLACK SILICONE TO THE BASE OF EACH PIGTAIL.

## MARK EACH CONNECTOR WITH PAINT PENS AS SHOWN


40

# SECTION 5

# WIRING HARNESS ASSEMBLY

41

## CUT 6 LENTHS OF 4-STRAND RIBBON WIRE TO THE

42

## FOLLOWING LENTHS:

### J1-WIRE = 40.6cm (16”) LONG

### J2-WIRE = 71cm (28”) LONG

### J3-WIRE = 71cm (28”) LONG

### J4-WIRE =86.3cm (34”) LONG

### J5-WIRE = 86.3cm (34”) LONG

### J6-WIRE = 132cm (52”) LONG


CONNECT 4 PIN FEMALE JST
CONNECTOR TO ONE END OF EACH WIRE AS OUTLINED IN SECTION 1.

## Use paint pens to mark each end of the motor wires as shown:

## CUT 6 LENTHS OF STRANDED RIBBON WIRE TO

45

## THE FOLLOWING LENTHS – STRIP OFF THE BLUE WIRE FROM EACH SO THAT YOU

HAVE 3 STRAND WIRES (RED,

### GREEN, BLACK):

### J1-WIRE = 71cm (16”) LONG

### J2-WIRE = 58.4cm (23”) LONG

### J3-WIRE = 86.4cm (34”) LONG

### J4-WIRE =86.4cm (34”) LONG

### J5-WIRE = 132cm (52”) LONG

### J6-WIRE = 132cm (52”) LONG

### THES 6 WIRES WILL BE FOR THE

LIMIT SWITCHES.


STRIP 6mmTO 8mm FROM THE OTHER END OF THE LIMIT SWITCH WIRES

INSTALL 3 PIN FEMALE JST CONNECTOR AS OUTLINED IN SECTION 2 ON THE END OF EACH OF THE 6 LIMIT SWITCH WIRES.

USE RED PAINT PEN TO MARK THE J3 LIMIT SWITCH WIRE AT BOTH ENDS AS SHOWN.

USE BLUE PAINT PEN TO MARK THE J2 LIMIT SWITCH WIRE AT BOTH ENDS AS SHOWN.

NOTE: AS BEFORE THE J1 WIRE DOES NOT NEED TO BE MARKED.


USE WHITE PAINT PEN TO MARK THE J5 LIMIT SWITCH WIRE AT BOTH ENDS AS SHOWN.

NOTE: AS BEFORE THE J6 WIRE DOES NOT NEED TO BE MARKED.

USE YELLOW PAINT PEN TO MARK THE J4 LIMIT SWITCH WIRE AT BOTH ENDS AS SHOWN.

PULL ALL MOTOR AND LIMIT SWITCH WIRE ENDS THROUGH PG16 GLAND NUT AS SHOWN

USE STEPPED BIT TO DRILL 7/8” HOLE IN END OF PROJECT BOX.

PULL LIMIT SWITCH WIRES FAR ENOUGH OUT OF BOX TO GIVE
YOURSELF SOME ROOM TO WORK. ON THE STRIPPED END OF LIMIT SWITCH WIRES – SEPARATE THE WIRE STRANDS THEN TWIST ALL THE RED WIRES TOGETHER AND THEN TWIST ALL THE BLACK WIRES TOGETHER.

INSTALL WIRE LOOM AND GLAND NUT INTO PROJECT BOX AS SHOWN.


CUT OFF MALE END OF RJ45
EXTENSION WIRE AND STRIP OFF OUTER SHEETHING AS SHOWN.

SLIP 2.5cm (1”) LENGTH OF 6mm HEAT SHRINK TUBING OVER RED AND BLACK WIRE BUNDLES.

SLIP 2.5cm (1”) LENGTH OF 2mm HEAT SHRINK TUBING OVER EACH OF THE GREEN WIRES.

SOLDER BROWN WIRE FROM RJ45 TO THE GROUP OF RED WIRES AS SHOWN.

THE FOLLOWING STEPS WILL
CONNECT THE GREEN LIMIT SWITCH WIRES TO THE CORRECT RJ45 WIRES. THE IMAGE TO THE LEFT SHOWS THE COLOR CODE FOR WHICH RJ45 WIRE GOES TO WHICH LIMIT SWITCH

J1 = WHITE / ORANGE STRIPE
J2 = ORANGE / WHITE STRIPE J3 = WHITE / GREEN STRIPE
J4 = BLUE / WHITE STRIPE
J5 = WHITE / BLUE STRIPE
J6 = GREEN / WHITE STRIPE
COMMON NEGATIVE = WHITE / BROWN STRIPE.
COMMON POSITIVE = BROWN / WHITE STRIPE.


SOLDER WHITE / BROWN STRIPE WIRE TO THE GROUP OF BLACK WIRES.

SLIDE HEAT SHRINK TUBE OVER SOLDER JOINT AND USE HEAT GUN TO SHRINK TUBE.

TRACE UNPAINTED GREEN WIRE FROM SHORT J1 LIMIT SWITCH WIRE AND SOLDER TO THE WHITE / ORANGE STRIPE WIRE.

THEN SLIDE HEAT SHRINK TUBE OVER SOLDER JOINT AND SHRINK WITH HEAT GUN.

SLIDE HEAT SHRINK TUBE OVER SOLDER JOINT AND USE HEAT GUN TO SHRINK TUBE.

FIND THE J3 LIMIT SWITCH WIRE
WHICH WAS MARKED WITH RED PAINT PEN AND SOLDER TO THE WHITE / GREEN STRIPE WIRE.

THEN SLIDE HEAT SHRINK TUBE OVER SOLDER JOINT AND SHRINK WITH HEAT GUN.

FIND THE J2 LIMIT SWITCH WIRE WHICH WAS MARKED WITH BLUE PAINT PEN AND SOLDER TO THE ORANGE / WHITE STRIPE WIRE.

THEN SLIDE HEAT SHRINK TUBE OVER SOLDER JOINT AND SHRINK WITH HEAT GUN.


FIND THE J5 LIMIT SWITCH WIRE WHICH WAS MARKED WITH WHITE PAINT PEN AND SOLDER TO THE WHITE / BLUE STRIPE WIRE.

THEN SLIDE HEAT SHRINK TUBE OVER SOLDER JOINT AND SHRINK WITH HEAT GUN.

FIND THE J4 LIMIT SWITCH WIRE WHICH WAS MARKED WITH YELLOW PAINT PEN AND SOLDER TO THE BLUE / WHITE STRIPE WIRE.

THEN SLIDE HEAT SHRINK TUBE OVER SOLDER JOINT AND SHRINK WITH HEAT GUN.

SLIDE THE LARGE 10mm HEAT SHRINK TUBE OVER THE ENTIRE BUNDLE OF JOINTS AND USE HEAT SHRINK GUN TO SHRINK TUBING.

FIND THE REMAINING J6 LIMIT SWITCH WIRE WHICH WAS NOT MARKED AND SOLDER TO THE GREEN / WHITE STRIPE WIRE.

THEN SLIDE HEAT SHRINK TUBE OVER SOLDER JOINT AND SHRINK WITH HEAT GUN.


Use drill bit and rotary tool bit to create a square hole at end opposite the 6 holes as shown. Hole should be 7/8” x 3/4” to accept the RJ45 panel mount plug.

USE STEPPED BIT TO DRILL (x6) 5/8” diameter holes evenly spaced as shown.

Holes are 7/8” from edges and 1” apart.

Solder the J1 motor wires to the back side of aviation plug as shown.

Looking at the back of the connector solder the black wire to upper left , green wire upper right, red wire to lower left and the blue wire to lower right.

Install (x6) male side 4pin aviation plugs and (x1) RJ45 panel mount jack as shown in project box cover.

Install RJ45 plug into panel socket.

Solder the remaining motor wires to aviation plugs as shown.


Work10mm wire wrap under gland nut and into gland.

Carefully pull wire slack out and install cover on project box.

Use digital multi meter to test continuity on every pin of every motor wire and every limit switch wire.

Tighten gland nut.


IF YOU WILL BE USING A PNEUMATIC GRIPPER LAY PNEUMATIC LINES ALONG WITH WIRE BUNDLES. THE PNEUMATIC LINES CAN BE AS LONG AS YOU WANT BUT MAKE SURE THE PNEUMATIC LINES EXTEND APPROX 8” PAST THE J6 CONNECTORS AT THE VERY END OF THE HARNESS.

WRAP BUNDLE WITH 10mm SPIRAL WRAP AS SHOWN –WHEN YOU ARE 15.25cm (6”) FROM END OF ENCLOSURE PULL THE J1 MOTOR AND LIMIT WIRES OUT OF THE BUNDLE.

CONTINUE WRAPPING SPIRAL WRAP PAST THE SPOT WHERE THE J1 WIRES EXIT THE WRAP – THEN ATTACH A MOUNTING CABLE TIE AS SHOWN.

CONTINUE WRAPING BUNDLE WITH SPIRAL WRAP –WHEN YOU ARE 40.5cm (16”) FROM ATX CONNECTOR PULL THE J2 MOTOR AND LIMIT WIRES AS WELL AS THE J2 MOTOR OUT OF THE WRAP AS SHOWN.

CONTINUE WRAPPING BUNDLE WITH SPIRAL WRAP –WHEN YOU GET JUST PAST 69cm FROM ATX CONNECTOR BREAK THE J4 AND J5 MOTOR CONNECTORS AND J2 AND J4 LIMIT CONNECTORS OUT OF THE WRAP. THEN PLACE A MOUNTING CABLE TIE 68.5cm FROM ATX CONNECTOR.

CONTINUE WRAPPING BUNDLE AND PLACE ANOTHER MOUNTING CABLE TIE 15.25cm (6”) FROM PREVIOIUS CABLE TIE.


CONTINUE WRAPPING SPIRAL WRAP ALL THE WAY TO THE J6 CONNECTORS AS SHOWN. INSTALL MOUNTING CABLE TIE AT END OF SPIRAL WRAP AS SHOWN.

GO BACK TO THE J2 & 3 MOTOR AND LIMIT WIRES THAT EXIT THE LOOM AND WRAP THEM IN SPIRAL WRAP AND THEN WRAP THE JOINT WITH ELECTRICAL TAPE AS SHOWN.

## WIRING HARNESS IS NOW COMPLETE

67

# SECTION 6

# WIRING HARNESS INSTALLATION

68


SECURE THE HARNESS TO THE J2 ARM USING M4 SCREWS THROUGH THE CABLE TIE MOUNTS AS SHOWN.

SECURE HARNESS TO BASEPLATE USING M4 SCREW ANDTHEN CONNECT THE J1 MOTOR AND LIMIT SWITCH
CONNECTORS.

CONNECT THE J2 & J3 MOTOR
CONNECTORS AND THE J2 LIMIT SWITCH CONNECTOR AS SHOWN.

ROUTE THE J2 & J3 MOTOR AND LIMIT SWITCH WIRES THROUGH THE CENTER OF ROBOT AND THEN SECURE TO THE J2 MOTOR SUPPORT PLATE USING A STANDARD CABLE TIE THROUGH THE SIDE HOLE AS SHOWN.

THE CABLE TIE SHOULD REMAIN LOOSE AROUND THE WIRES – JUST TIGHT ENOUGH SO THE CONNECTORS CANT SLIP THROUGH THE TIE AND THE WIRES CANT SWING INTO THE J2 LIMIT SWITCH.

SECURE THE END OF THE HARNESS TO THE J5 SUPPORT ARM AS SHOWN USING A M4 SCREW AND THEN CONNECT THE J5 & J6 CONNECTORS AS WELL AS THE PNEUMATIC GRIPPER TUBES.

THIS CONCLUDES THE WIRING
HARNESS MANUAL – PLEASE VISIT THE PROJECT PAGE AND REVIEW THE VIDEO ON STARTUP AND
CALIBRATION.

CONNECT THE J4 & J5 MOTOR AND LIMIT SWITCH CONNECTORS AS SHOWN.

# SECTION 7

# MOTOR CABLES

72

Strip 10mm of outer sheathing off each end of cable.

You will need to make 6 cables for the robot and a 7th if you are building a travel track.

Cut each cable to whatever length you need – in this example I have cut each cable to 6’ long.


Pre apply solder to each contact on connector.

Strip 5mm sheathing off each wire and then tin each wire with solder as shown.

Cables are “straight through” -solder wires on each end of cable mirror image to the other as shown in the sketch and photo shown.

Solder wires to each contact on connector – see following steps for wire position.


Slide connector housing over connector and install screw.

Wrap electrical tape around solder joints to prevent any potential short on connector housing.

Repeat this process for each cable needed.

Tighten screws on wire clamp.

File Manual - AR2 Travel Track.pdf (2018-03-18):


# Model AR2 Travel Track

Travel Track
Manual | 1

### NOTE:

### This manual shows the construction of the AR2 travel track using 500mm length guides but you can build the track any length you want. Tack can be screw drive

as shown or you can design your own track or use a belt drive if desired.

### Any stepper motor can be used as long as its wired as shown and in the

electrical enclosure manual.

### - 3D printed components require all threaded holes to be cleared with

appropriate drill size.

### - All printed components were printed at minimum 50% solid at 2mm layer

height and thick shells.

# BILL OF MATERIALS

# Plastic Components


DRIVE MOUNT (x1) | BEARING SPACER (x2)
BLOCK SPACER (x4) | TEMPLATE (x1)

# Stepper Motors

# Stepper motors as well as stepper drivers and brackets are available from Stepper Online

# http://www.omc-stepperonline.com/


### NEMA 17 stepper motor SKU: 17HS19-2004S1

### NEMA 17 bracket SKU: ST-M1

# Hardware


Qty.(1) T8 lead screw with bearing blocks and coupler - Amazon

Qty.(1) 12mm linear slide with bearings -Amazon


### Electrical project box (x1)

### PG7 gland nut (x1)


### GX-16 aviation plug (x1)

### 12” x 6” x ¼” aluminum plate (x1)- McMaster Carr

# ASSEMBLY


Place template on corner of aluminum plate as shown and then use spring loaded center punch to mark the 4 holes. Rotate and flip template to each corner and repeat until all 16 holes are marked.

Drill all 16 holes to clearance 5mm screw.

Countersink all 16 holes. | Draw centerline on aluminum plate as shown.


Place drive mount on plate aligned on centerline. Use spring loaded center punch to mark (x4) holes.

Drill and tap (x4) M4 holes as shown.

Center J1 support spacer as shown and mark (x4) mounting holes.

Drill and tap (x4) M8 holes as shown.


Drill and tap (x2) M4 holes centered 30mm apart and 30mm from edge as shown.

When complete aluminum plate should be drilled as shown in this drawing.


Install (x4) linear bearings with block spacers between auminum plate and bearing as shown. Secure with (x16) M5x20 flat head screws. (do not fully tighten M5 screws yet)

Install T8 nut into drive mount as shown and secure with (x4) #2 screws.

Secure drive mount assembly to aluminum plate as shown using (x4) M4x20 socket head cap screws.

Use square to align tracks and then install one screw in right upper track securing it to worktable.


With platform slid to right end install one more screw in lower track.

Slide platform to other end and secure each rail to worktable.

Make sure platform glides easily from end to end and then install all remaining screws to secure rails to worktable.

Install T8 screw, bearing and motor coupler as shown.


With platform at maximum travel to the left side secure lead screw bearing and bearing spacer to work table as shown.

Tighten bearing and coupler set screws.


Turn screw manually and drive platform to far end. Secure opposite lead screw bearing and bearing spacer as shown at very end of screw.

Tighten bearing set screws.


Note that the drive mount should bottom out against the bearing and not allow the platform to go off the end of the rails.


Make sure platform moves smoothly and easily down rails and then tighten the (x16) M5 screws securing platform to rail bearings.


Temporarily install motor and bracket and use pencil to mark motor mount location.

Remove motor and secure motor mount to work table as shown.

Reinstall motor using (x4) M3x10 socket head cap screws.

Tighten shaft coupler set screws.

Install PG7 gland nut in side of enclosure as shown. Also drill 2 mounting holes in bottom of enclosure.


Wrap base of motor wires with spiral wrap.

Feed wires and spiral wrap through gland nut and secure enclosure to worktable as shown.

Install aviation plug in enclosure faceplate as shown.

Solder motor wires as shown to back side of aviation plug. (see next step)


Secure enclosure panel to project box as shown.

Secure robot to platform using (x4) M8x35 metric bolts.

Drill 5mm holes 30mm apart in bottom of enclosure and mount to back of platform as shown.

## Travel Track assembly is now complete. Please review the wiring harness, electrical enclosure and startup

manuals to complete the build.

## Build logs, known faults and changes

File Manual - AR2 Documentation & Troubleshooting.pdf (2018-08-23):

AR2 Robot Documentation

- Reach – 24.75 inches (62.9cm)
- Payload – 4.15 lbs (1.9kg)
- Accuracy - .01mm
- Repeatability - .75mm

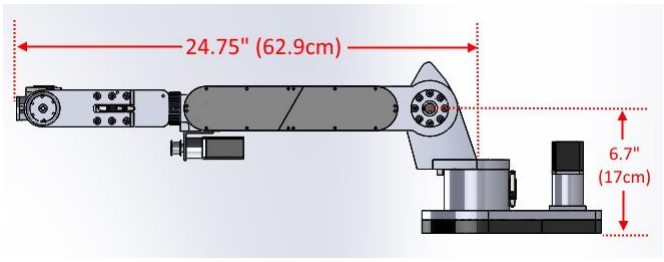
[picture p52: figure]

AR2 Robot Startup & Troubleshooting

Please start by watching the startup calibration video series starting with this video: https://www.youtube.com/watch?v=MMESgfq2Mjg

- Before powering up your control box double check all connections per the wiring schematic.
- Check continuity on all wiring harness connectors for each motor and each limit switch. It is imperative that all wire connectors are crimped carefully and checked.
- After powering up your control box use a multi meter to verify you have +5vdc to pulse and direction terminals on each driver.
- Manually depress each limit switch on robot and verify Arduino LED illumines when each switch is pressed.
- LED should go from dark to bright and should not be dim or partially lit. If this is not the case you likely have a switch shorted or crossed.

- Verify limit switches are wired such that they provide the Arduino pins a -5vdc signal when at rest and +5vdc when the switch is depressed.
- Before attempting to auto calibrate the robot jog each axis using joint mode a small amount in each direction.
- Verify each joint is jogging the correct direction per the joint direction drawings at the end of this document.
- If a particular joint jogs the same direction regardless of pressing the + or – direction buttons you likely have a wiring issue with the direction wire from the Arduino to the driver.
- If a joint does not move at all but others do you likely have an issue with the step wire from the Arduino to the driver.
- Do not use the auto calibrate button the first time, calibrate each joint one at a time using the individual joint calibration buttons.
- Have your hand on the E-Stop button the first time so that you can stop the robot and cut power to the drivers if there is an issue with each limit switch and the robot tries to overdrive the joint.
- You can also manually trigger the switch with your finger before the robot contacts the switch to give you extra time to hit the E-Stop in the event the robot doesn’t stop moving when the switch is made.
- Once all joints and switches are verified to be stopping and calibrating you can then use the auto calibrate to calibrate all joints at the same time.

Axis Directions

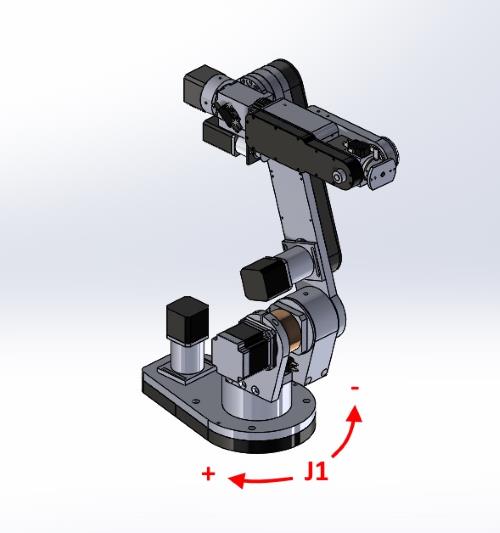
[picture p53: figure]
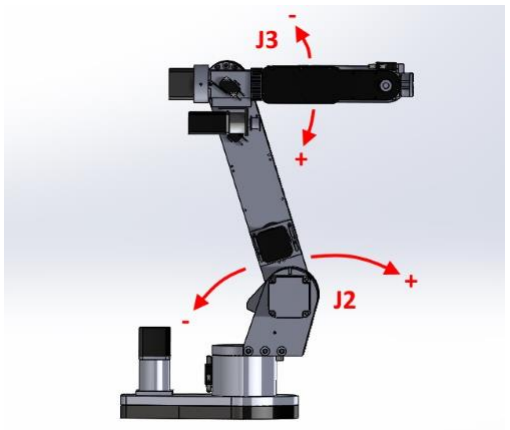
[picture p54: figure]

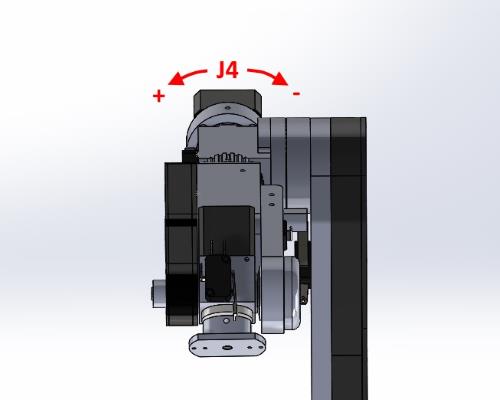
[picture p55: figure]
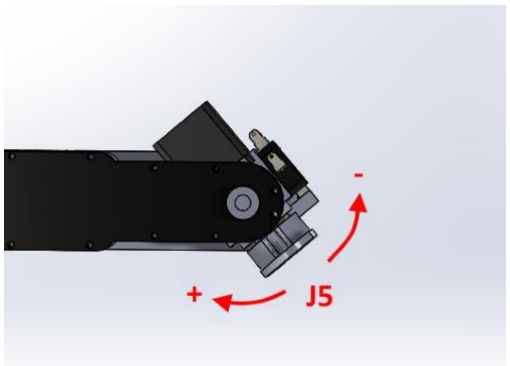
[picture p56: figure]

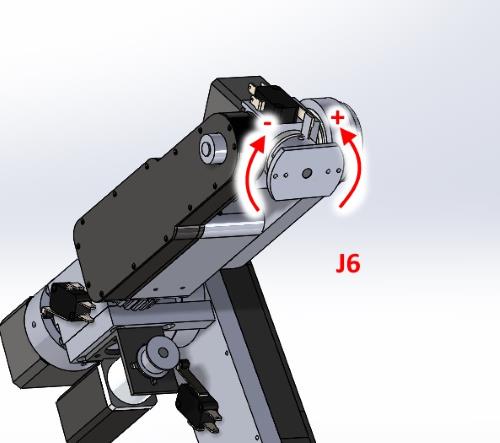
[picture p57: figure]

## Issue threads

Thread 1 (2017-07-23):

3D cad file

quangphuc91, 2017-07-23:
Very nice project

Can you send me step file , because my 3d printer can't printing more than 200mm, i need step file to split more part have dimension less than 200 mm

Thanks you

oconnorhorrill, 2017-07-23:
Hi Chris,

think you may have send this email to the wrong address. The AR2 is a great
project.

Kind regards,

Jim O’Connorhorrill.

On Sun, Jul 23, 2017 at 4:58 PM, quangphuc91 <notifications@github.com>
wrote:

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

Chris-Annin, 2017-07-24:
im sorry I ddint get a chance to reply - busy weekend.  I have had many
people ask for the step files - I havnt posted them yet as when we started
bulding the aluminum version of this robot we found some unexpected
differences in the bearing models.  I found the same issues in my plastic
prints and I made adjustements to the models I was using for printing but I
have not yet made any adjustments to the models I sent my machinist as he
is confirming exact changes that need to be made - so basically what im
saying is I have 2 different sets of models, a set for the aluminum version
and a set for the printed version.  Ive been telling everyone they need to
wait for me to finish working the bugs out on the aluminum models before I
can share them.  If you only need models for 3D printing I can sent you
what I have - just understand they wont be perfect if you try to use them
for machining as I have made many little adjustments to get them to print
out perfectly.   I will email you the models when I get home from work
tonight.  Its been a very hectic day so feel free to send me a reminder
email tonight if I dont get to it right away.

Chris

On Sun, Jul 23, 2017 at 4:38 PM, oconnorhorrill <notifications@github.com>
wrote:

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

Chris-Annin, 2017-07-25:
will .sldprt files work?  I haven't converted them to step files yet.  message me at chris.annin@gmail.com

quangphuc91, 2017-07-25:
yes , can you send me step file , b/c im using solidwork 2014 sp5

Vào Th 3, 25 thg 7, 2017 lúc 09:28 Chris Annin <notifications@github.com>
đã viết:

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
--
Tran Quang Phuc
PIP Department, Foster Electric Da Nang Company, Limited
Mobile: (+84)935294991
Address: Street 1, Hoa Cam Industrial Zone, Cam Le District, Da Nang City,
Vietnam
Site: www.foster-electric.com
Email: quangphuc91@gmail.com - vtqp@int.foster.com.vn
<quangphuc91@gmail.com+-+phuc.tranquang@fvd.foster.com.vn>

alfredanil, 2017-07-25:
Would be helpfull if the step files or solidworks files are uploaded/added to the main project.

quangphuc91, 2017-07-25:
thank you very much

Vào Th 3, 25 thg 7, 2017 lúc 15:32 Anil Kumar <notifications@github.com> đã
viết:

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
--
Tran Quang Phuc
PIP Department, Foster Electric Da Nang Company, Limited
Mobile: (+84)935294991
Address: Street 1, Hoa Cam Industrial Zone, Cam Le District, Da Nang City,
Vietnam
Site: www.foster-electric.com
Email: quangphuc91@gmail.com - vtqp@int.foster.com.vn
<quangphuc91@gmail.com+-+phuc.tranquang@fvd.foster.com.vn>

Chris-Annin, 2017-08-03:
step files are now posted on the project page.

On Tue, Jul 25, 2017 at 2:44 AM, quangphuc91 <notifications@github.com>
wrote:

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

Chris-Annin, 2017-08-03:
step files are now posted on the project page.

On Sun, Jul 23, 2017 at 4:38 PM, oconnorhorrill <notifications@github.com>
wrote:

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

Chris-Annin, 2017-08-03:
step files are now posted on the project page.

On Sat, Jul 22, 2017 at 11:58 PM, quangphuc91 <notifications@github.com>
wrote:

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

aaron02, 2017-10-12:
can i use the current files to made on of these out of aluminium ? or is this still in progress?

great roject :)

Chris-Annin, 2017-10-13:
yes the step files are good to go.  also read the notes on page 2 of the assembly manual.

conor87, 2017-12-11:
Can you publish Assembly file in step?
Project is brilliant and description is very well but with assy will be easier to build it.

Chris-Annin, 2017-12-11:
hellow,  just got the solidworks files posted a few days ago.  I can work
on rebuilding the assembly.  it got a little messy and I wanted to clean it
up.  I'll see what I can do to get the solidworks addembly together.

Chris

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

conor87, 2017-12-11:
This files are not compatible with solidworks 2015 (propably newer version), it's why I ask for step. If you are in assy enviroment, just save it as step and job is done :-)

conor87, 2017-12-11:
Question:
how it works with Python?
I love this language but since few weeks I try to work in Java. Main reason -> javafx. In Python GUI is still in the background.
Did you have any problems?

photoJames, 2018-03-19:
Couldn't find any files in the projects table. Would love to 3d print for the STEM lab I teach.

Chris-Annin, 2018-03-20:
3D print files are posted "3D print files.zip"   please let me know if any issues.

soswow, 2018-04-07:
> step files are now posted on the project page.
Where are those?

Closed 2018-03-20.

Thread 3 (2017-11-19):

How are you reducing play in the planetary gearboxes?

i-make-robots, 2017-11-19:
I received gearboxes from omc-stepperonline.com that claim 1 degree of play.  in practice it feels like more, but that might be my printer tolerances on this similar robot:  https://www.instagram.com/p/Ba68yt6AKv8/?taken-by=imakerobots

How are you reducing backlash/play?  Thanks!

Chris-Annin, 2017-11-20:
I agree,  Ive also found is slightly beyond 1°.  if opposing force is applied to the arm there is some backlash but with the robot under load or compression I have not had any issues and the robot repeats to position very well.   At some point in the future when I have more time I may look at designing the next generation/next size up robot with more expensive gearboxes (it will be substatially more - likely 5x to 7x price) but for now given size and budget I felt these motor/gearboxes were the most economical option I could find.

mdjurfeldt, 2017-11-23:
Could you estimate the position repeatability (in mm) for the plastic version and the aluminum version?

Chris-Annin, 2017-11-23:
Approx .075 to 1.5mm is what I have experienced in testing where I ran an exercise program several times and brought the robot back to a dial indicator to check repeatability.

Sent from my iPhone

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

Chris-Annin, 2017-11-24:
sorry for the delay.  I get alot of emails on the robot, difficult to keep
up.  .75mm is a good expectation - from what testing ive done.  keep in
mind these are very low cost gear boxes.  I think if I build next version
with high end gear boxes we could get alot better repeatablity.  but .75
isnt too bad for an inexpensive material handling unit.

On Thu, Nov 23, 2017 at 11:22 AM, mdjurfeldt <notifications@github.com>
wrote:

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

i-make-robots, 2017-11-24:
I found that the plastic parts I designed get chewed up at the motor shaft because they can't take the torque.  I'm currently using FEA to design some steel mounting adapters to relieve the strain.  How did you solve/avoid this issue?

Chris-Annin, 2017-11-25:
are you having trouble with parts for the AR2 robot? or are you saying you have other parts that are having issues?

on my robot I print any spindles that have key shafts requiring torque out of ABS at 100% solid, all spindles are pressed into or captured around the OD by a taper bearing - the steel bearing keeps the ABS compressed and doesn't allow it to displace or break apart and then lastly I make sure to buy key-stock the runs the entire length of the spindle to distribute load as far across the ABS as possible rather that a short piece of key.

thank you for the complement on the J5 drive - difficult to come up with low cost solutions to transfer motion 90° with the motor mounted at a distance without an expensive gear box,  It took me a couple days of contemplating before that one came to me.  Im thinking of using similar process for more joints on a larger scale for my next robot.

i-make-robots, 2017-11-25:
I would love to collaborate on a design.  My plastic problems are in this machine: https://www.instagram.com/p/Ba68yt6AKv8
which I have since updated to have no belts, no glue, and (at present) no metal parts that must be custom fabricated.  https://www.instagram.com/p/Bbvp4Ijgzs8/
The keys at the elbow and shoulder bite through the ABS, but I only printed it at 20% infill.  I will try it again at 100% and see if that works better.  My next option is a steel disc that couples the plastic to the shaft with bolts via six tapped holes on the disc.

i-make-robots, 2017-11-25:
It occurs to me that your J5 doesn't even need a closed loop belt, which will make sourcing and tensioning easier (maybe?)

Kristong, 2017-12-07:
I found that "J5 main bearing housing" in SolidWork files, the dimension is not correct !

Chris-Annin, 2017-12-09:
which dimension do you think is incorrect?

Kristong, 2017-12-09:
I'm do assembly your AR2 by your Solidworks files.
I found 2 parts ..
J5 main bearing housing.
J6 main bearing arm.

After I use J6 main bearing it correct., OK.
I don't know where J5 main bearing housing
, where to assembly. .?

Best regards,
Kristong S.

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

Closed 2018-03-20.

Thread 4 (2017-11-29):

Public support for AR2 project

Robot-rock, 2017-11-29:
I have decided to help with the accessibility of this project for others, as I am making this project myself. I will post any updates here in the hopes that I can reach more people, and limit the total required human effort to build a robotic arm. My ultimate goal is to lower the cost of robotics and enable it to become more of a tool that everyone can benefit from.

I will be making this out of aluminum. I have made a robotic torso that will hold 2 arms, J1 may be powered by wheelchair motors with gearboxes encoders mounted in place of stepper motors. This is because I already have the electrical control hardware, and because my modification is designed to work vertically.

In the meantime, I have organized a parts list for others to use.
Parts: http://a.co/4qjpU1v
Wiring: http://a.co/dorwtcY

Closed 2018-03-20.

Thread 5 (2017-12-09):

Missing screw holes in Base support part 1 and 2

Johansson-D, 2017-12-09:
Hi Chris_Annin.
I just joined this "little" project. :)
The M4 holes in the Base support part 1 and 2  are missing, or should one drill them?
The M4 holes are shown in the BOM pdf on page 3.

File names:
J1 base support spacer part 1 2017.09.18
J1 base support spacer part 2 2017.09.18

Best regards and THAN YOU for sharing this/
Dahniel

Chris-Annin, 2017-12-09:
hello, I was thinking perhaps they were not needed and just added extra
work and cost so I removed them from the models.  if you feel they are
needed I could put them back but I thought the 4 main mounting holes would
be sufficient but let me know what you think.

Chris

On Sat, Dec 9, 2017 at 3:07 AM, Johansson-D <notifications@github.com>
wrote:

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

Johansson-D, 2017-12-10:
Hi Chris,
thanks for a quick reply.
Are you saying that the M4 screw are not needed?
I would be glad if you could mail the files or put them up at the website
again. Because then one has the option of chosing.

Is this a hobby for you Chris, or do you work with robots?
I just started a two year master in robotics and automation and I love it.
Example of courses we have had so far are:
- Robot modeling using Matlab
- Robot simulation using ABB:s Robotstudio
- Robotsystem where we play with the real deal, seven ABB robots. 😀

Best regards,
Dahniel Johansson

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

Johansson-D, 2017-12-16:
Hi Chris.
Did you put up the files somewhere?
I feel that they are needed.
Best regards,
Dahniel

Chris-Annin, 2017-12-16:
I believe if you go to Code, then click on commits and go to may 29th 2017 and click view repository at this point in time you should find the earlier print files.

https://github.com/Chris-Annin/AR2/tree/20a7b994f84574137bca8c4c3074bd3974aa6010

Johansson-D, 2017-12-22:
I found them here:
https://github.com/Chris-Annin/AR2/blob/fe274c6ada36cc75682504b6163ea55a67c506cc/AR2%20print%20files.zip

Thx Chris

Chris-Annin, 2018-03-20:
updated design calls for (x2) 4mm dowels rather than wasted expense on many screws.

Closed 2018-03-20.

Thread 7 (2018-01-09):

Could you add more comments in sketch_Annin_Robot.ino ?

cqliliping, 2018-01-09:
Hi.Chris_Annin.
I'm reading  arduino code,but it is too difficult to me to comprehend somewhere in short time.especially in code line 831 ////CALC SPEEDS///// ,/////DRIVE MOTORS/////. I want to know how it works,then I can make every stepper works on the same speed with different pulse.
I'm from China and interesting in this project,and learning it.I just hope everyone can understand it rapidly and practice.
Best regards
liliping

Chris-Annin, 2018-01-10:
hi.  below is my algorithm.  first i find which motor has the most steps
and that is called high step, then I divide each of the other motor steps
into high step to figure out which loops of the while statement to pulse
the motor on.  the motor with highest step pulses the motor every loop -
the other motors will only pulse on certain loops based on the divide.  it
will not divide evenly there is always left over so I take the remainder
and then run a calculation to spread these leftovers evenly across the span
of high step and then I skip these loops, and then I do it again to catch
any more leftovers and create a 3rd level of skips.  its confusing but you
will have to study the code below.  PE stands for Pulse Every (loop) and SE
stands for Skip Every (loop).  I will try to add more comments next time i
make a rev change.  thank you.

        //FIND HIGHEST STEP
        int HighStep = J1step;
        if (J2step > HighStep)
        {
          HighStep = J2step;
        }
        if (J3step > HighStep)
        {
          HighStep = J3step;
        }
        if (J4step > HighStep)
        {
          HighStep = J4step;
        }
        if (J5step > HighStep)
        {
          HighStep = J5step;
        }
        if (J6step > HighStep)
        {
          HighStep = J6step;
        }

        int J1_PE = 0;
        int J2_PE = 0;
        int J3_PE = 0;
        int J4_PE = 0;
        int J5_PE = 0;
        int J6_PE = 0;

        int J1_SE_1 = 0;
        int J2_SE_1 = 0;
        int J3_SE_1 = 0;
        int J4_SE_1 = 0;
        int J5_SE_1 = 0;
        int J6_SE_1 = 0;

        int J1_SE_2 = 0;
        int J2_SE_2 = 0;
        int J3_SE_2 = 0;
        int J4_SE_2 = 0;
        int J5_SE_2 = 0;
        int J6_SE_2 = 0;

        int J1_LO_1 = 0;
        int J2_LO_1 = 0;
        int J3_LO_1 = 0;
        int J4_LO_1 = 0;
        int J5_LO_1 = 0;
        int J6_LO_1 = 0;

        int J1_LO_2 = 0;
        int J2_LO_2 = 0;
        int J3_LO_2 = 0;
        int J4_LO_2 = 0;
        int J5_LO_2 = 0;
        int J6_LO_2 = 0;

        //reset
        int J1cur = 0;
        int J2cur = 0;
        int J3cur = 0;
        int J4cur = 0;
        int J5cur = 0;
        int J6cur = 0;

        int J1_PEcur = 0;
        int J2_PEcur = 0;
        int J3_PEcur = 0;
        int J4_PEcur = 0;
        int J5_PEcur = 0;
        int J6_PEcur = 0;

        int J1_SE_1cur = 0;
        int J2_SE_1cur = 0;
        int J3_SE_1cur = 0;
        int J4_SE_1cur = 0;
        int J5_SE_1cur = 0;
        int J6_SE_1cur = 0;

        int J1_SE_2cur = 0;
        int J2_SE_2cur = 0;
        int J3_SE_2cur = 0;
        int J4_SE_2cur = 0;
        int J5_SE_2cur = 0;
        int J6_SE_2cur = 0;

        int highStepCur = 0;

        ///// DRIVE MOTORS /////
        while (J1cur < J1step || J2cur < J2step || J3cur < J3step || J4cur
< J4step || J5cur < J5step || J6cur < J6step)
        {

          /////// J1 ////////////////////////////////
          ///find pulse every
          J1_PE = (HighStep / J1step);
          ///find left over 1
          J1_LO_1 = (HighStep - (J1step * J1_PE));
          ///find skip 1
          if (J1_LO_1 > 0)
          {
            J1_SE_1 = (HighStep / J1_LO_1);
          }
          else
          {
            J1_SE_1 = 0;
          }
          ///find left over 2
          if (J1_SE_1 > 0)
          {
            J1_LO_2 = HighStep - ((J1step * J1_PE) + ((J1step * J1_PE) /
J1_SE_1));
          }
          else
          {
            J1_LO_2 = 0;
          }
          ///find skip 2
          if (J1_LO_2 > 0)
          {
            J1_SE_2 = (HighStep / J1_LO_2);
          }
          else
          {
            J1_SE_2 = 0;
          }
          ////////////////////////
          if (J1cur < J1step)
          {
            if (J1_SE_2 == 0)
            {
              J1_SE_2cur = (J1_SE_2 + 1);
            }
            if (J1_SE_2cur != J1_SE_2)
            {
              J1_SE_2cur = ++J1_SE_2cur;
              if (J1_SE_1 == 0)
              {
                J1_SE_1cur = (J1_SE_1 + 1);
              }
              if (J1_SE_1cur != J1_SE_1)
              {
                J1_SE_1cur = ++J1_SE_1cur;
                J1_PEcur = ++J1_PEcur;
                if (J1_PEcur == J1_PE)
                {
                  J1cur = ++J1cur;
                  J1_PEcur = 0;
                  digitalWrite(J1stepPin, LOW);
                }
              }
              else
              {
                J1_SE_1cur = 0;
              }
            }
            else
            {
              J1_SE_2cur = 0;
            }
          }
          /////////////////////////////////////////

          /////// J2 ////////////////////////////////
          ///find pulse every
          J2_PE = (HighStep / J2step);
          ///find left over 1
          J2_LO_1 = (HighStep - (J2step * J2_PE));
          ///find skip 1
          if (J2_LO_1 > 0)
          {
            J2_SE_1 = (HighStep / J2_LO_1);
          }
          else
          {
            J2_SE_1 = 0;
          }
          ///find left over 2
          if (J2_SE_1 > 0)
          {
            J2_LO_2 = HighStep - ((J2step * J2_PE) + ((J2step * J2_PE) /
J2_SE_1));
          }
          else
          {
            J2_LO_2 = 0;
          }
          ///find skip 2
          if (J2_LO_2 > 0)
          {
            J2_SE_2 = (HighStep / J2_LO_2);
          }
          else
          {
            J2_SE_2 = 0;
          }
          ////////////////////////
          if (J2cur < J2step)
          {
            if (J2_SE_2 == 0)
            {
              J2_SE_2cur = (J2_SE_2 + 1);
            }
            if (J2_SE_2cur != J2_SE_2)
            {
              J2_SE_2cur = ++J2_SE_2cur;
              if (J2_SE_1 == 0)
              {
                J2_SE_1cur = (J2_SE_1 + 1);
              }
              if (J2_SE_1cur != J2_SE_1)
              {
                J2_SE_1cur = ++J2_SE_1cur;
                J2_PEcur = ++J2_PEcur;
                if (J2_PEcur == J2_PE)
                {
                  J2cur = ++J2cur;
                  J2_PEcur = 0;
                  digitalWrite(J2stepPin, LOW);
                }
              }
              else
              {
                J2_SE_1cur = 0;
              }
            }
            else
            {
              J2_SE_2cur = 0;
            }
          }
          /////////////////////////////////////////

          /////// J3 ////////////////////////////////
          ///find pulse every
          J3_PE = (HighStep / J3step);
          ///find left over 1
          J3_LO_1 = (HighStep - (J3step * J3_PE));
          ///find skip 1
          if (J3_LO_1 > 0)
          {
            J3_SE_1 = (HighStep / J3_LO_1);
          }
          else
          {
            J3_SE_1 = 0;
          }
          ///find left over 2
          if (J3_SE_1 > 0)
          {
            J3_LO_2 = HighStep - ((J3step * J3_PE) + ((J3step * J3_PE) /
J3_SE_1));
          }
          else
          {
            J3_LO_2 = 0;
          }
          ///find skip 2
          if (J3_LO_2 > 0)
          {
            J3_SE_2 = (HighStep / J3_LO_2);
          }
          else
          {
            J3_SE_2 = 0;
          }
          ////////////////////////
          if (J3cur < J3step)
          {
            if (J3_SE_2 == 0)
            {
              J3_SE_2cur = (J3_SE_2 + 1);
            }
            if (J3_SE_2cur != J3_SE_2)
            {
              J3_SE_2cur = ++J3_SE_2cur;
              if (J3_SE_1 == 0)
              {
                J3_SE_1cur = (J3_SE_1 + 1);
              }
              if (J3_SE_1cur != J3_SE_1)
              {
                J3_SE_1cur = ++J3_SE_1cur;
                J3_PEcur = ++J3_PEcur;
                if (J3_PEcur == J3_PE)
                {
                  J3cur = ++J3cur;
                  J3_PEcur = 0;
                  digitalWrite(J3stepPin, LOW);
                }
              }
              else
              {
                J3_SE_1cur = 0;
              }
            }
            else
            {
              J3_SE_2cur = 0;
            }
          }
          /////////////////////////////////////////

          /////// J4 ////////////////////////////////
          ///find pulse every
          J4_PE = (HighStep / J4step);
          ///find left over 1
          J4_LO_1 = (HighStep - (J4step * J4_PE));
          ///find skip 1
          if (J4_LO_1 > 0)
          {
            J4_SE_1 = (HighStep / J4_LO_1);
          }
          else
          {
            J4_SE_1 = 0;
          }
          ///find left over 2
          if (J4_SE_1 > 0)
          {
            J4_LO_2 = HighStep - ((J4step * J4_PE) + ((J4step * J4_PE) /
J4_SE_1));
          }
          else
          {
            J4_LO_2 = 0;
          }
          ///find skip 2
          if (J4_LO_2 > 0)
          {
            J4_SE_2 = (HighStep / J4_LO_2);
          }
          else
          {
            J4_SE_2 = 0;
          }
          ////////////////////////
          if (J4cur < J4step)
          {
            if (J4_SE_2 == 0)
            {
              J4_SE_2cur = (J4_SE_2 + 1);
            }
            if (J4_SE_2cur != J4_SE_2)
            {
              J4_SE_2cur = ++J4_SE_2cur;
              if (J4_SE_1 == 0)
              {
                J4_SE_1cur = (J4_SE_1 + 1);
              }
              if (J4_SE_1cur != J4_SE_1)
              {
                J4_SE_1cur = ++J4_SE_1cur;
                J4_PEcur = ++J4_PEcur;
                if (J4_PEcur == J4_PE)
                {
                  J4cur = ++J4cur;
                  J4_PEcur = 0;
                  digitalWrite(J4stepPin, LOW);
                }
              }
              else
              {
                J4_SE_1cur = 0;
              }
            }
            else
            {
              J4_SE_2cur = 0;
            }
          }
          /////////////////////////////////////////
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
cqliliping, 2018-01-10:
hi,Chris-Annin.
'PE stands for Pulse Every (loop) and SE stands for Skip Every (loop)' help me a to understand more with it,Maybe  need to make a record when I study the code.
Thanks for your reply!
liliping

Closed 2018-03-20.

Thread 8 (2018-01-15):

motor driver

Nikolastesla66, 2018-01-15:
Hello Annin I am very interested in your robot.
I want to rebuild the AR2.
Currently I can not find the motor driver board (st-6600) on the internet.
Since I am very new to this field, I do not know what I can take instead.
Is it possible to install the digital motor drivers?
I would be extremely happy if you answered me.

Chris-Annin, 2018-01-15:
take a look at the manual for the electrical enclosure - this has info for
the digital drivers.  in the latest robot I made I used five DM542T and one
DM320T drivers

On Mon, Jan 15, 2018 at 9:30 AM, Nikolastesla66 <notifications@github.com>
wrote:

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

Chris-Annin, 2018-03-20:
I eliminated the ST-6600 from the BOM as they are obsolete, please use the DM-542T and DM-320T or any driver of your choice.  doesnt matter too much as long as the micro stepping is set correctly and amperage is correct.

Closed 2018-03-20.

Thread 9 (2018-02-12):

STEP-files for 3D-printed version

Knechtie, 2018-02-12:
Hi,
could you also provide the STEP files for the 3D-printed version?
I've noticed some differences between the .stl files of the 3D-printed version and the step files (aluminum version, I guess?).

Thank You!

Chris-Annin, 2018-02-12:
which files specifically do you see differences?  I did make minor
adjustments to the .stl files to accomodate for shrink issues especially on
some of the bearing diameters but I left the step files unmodified for use
in machining purposes - are you looking at the small differences for shrink
or are you talking about the different files for the initial design with
ecomonmy series motors and the spring assist.  I am in the process of
updating the design so the printed and aluminum are identical.  I need
to print and put together another printed robot - I am discontiuing use of
the economy motors for J123 and also eliminating the spring I think
depending if the J2 spindle can support load without spring assist but I
need to print and test another robot.  I will try to get this done as soon
as I can and get all the files updated.

Chris

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

Chris-Annin, 2018-03-20:
email me at chris.annin@gmail.com and I will try to get you the files you need.

machinekoder, 2018-06-24:
Where can I find the STEP files?

Closed 2018-03-20.

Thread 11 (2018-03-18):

Go To Fine Calibration Position Button

jeffmaeder, 2018-03-18:
The button on the new version 1.4 is not executing a move to position like in the 1.1 software.

Chris-Annin, 2018-03-19:
can you tell me more? which button?

On Sun, Mar 18, 2018 at 8:35 AM, jeffmaeder <notifications@github.com>
wrote:

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

Chris-Annin, 2018-03-19:
I think I see the issue.  im on it.  I'll let you know when I have a fix.

Chris-Annin, 2018-03-20:
posted updated files.  I believe the bug is fixes as I havnt been able to recreate after.  please confirm

Chris-Annin, 2018-03-21:
Ok I’ll look again I must be missing something obvious. Thank you for your help and pointing this out.

Sent from my iPhone

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

Closed 2018-03-20.

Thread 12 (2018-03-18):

CAD Files for new Version

BauerPh, 2018-03-18:
Hi,
At first many thanks for your new version.
Would you provide the CAD files for the new 3D printed version?
We need them to built your robot within a school project at a german school for automation technologies.

Thanks in advance.

Chris-Annin, 2018-03-19:
what files do you need?  with the kickstarter trying to launch aluminum
kits i havnt posted the step files. do you need solidworks files or step
files?

On Sun, Mar 18, 2018 at 10:32 AM, Philipp Bauer <notifications@github.com>
wrote:

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

BauerPh, 2018-03-19:
solidworks assembly would be great!

BauerPh, 2018-03-19:
And 2 another questions:
- The ATX connector is not required anymore? Because it is still listed in the BOM.
- What is the advantage of the chain option inatead a belt?

Chris-Annin, 2018-03-20:
email me at chris.annin@gmail.com and I will try and get you the files you need.

Chris-Annin, 2018-03-20:
I did switch from ATX to aviation plugs and separate wires as this makes it more practical to make cables of any length you need.  I removed the ATX cable from the design - I just updated the wiring harness manual and removed it from the BOM -thanks for pointing that out.

The belt was stretching too much so I opted for the chain.

soswow, 2018-04-07:
@Chris-Annin I am just curious why those CAD files are not part of a repo?

Closed 2018-03-20.

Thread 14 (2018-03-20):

Excel typo?

TadyTheFish, 2018-03-20:
Not really an issue. Maybe i'm missing something so please correct me if i'm wrong.

In the excel spreadsheet and on the inverse kinematic section, cell N3 says degrees. should't it say mm or delta mm?

Chris-Annin, 2018-03-21:
you are correct that should be mm.  ive updated a few things in the model and in a few weeks I will post another video in the kinematic series to cover changes.  thank you.
Chrhis

Closed 2018-03-21.

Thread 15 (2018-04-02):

gripper

Isergix, 2018-04-02:
I do not understand how the gripper works. It is a pneumatic gripper. Does it work with air? Thank you.

Chris-Annin, 2018-04-02:
Yes, it’s a pneumatic gripper controlled with a 5 port solenoid valve (see robot bill of material in construction manual), this valve is 24vdc driven by one of the robots 8 relay outputs.

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

Closed 2018-04-04.

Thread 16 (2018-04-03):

Screen Size on Notebook

projectholder, 2018-04-03:
Hi Chris

Do you  have an idea why my screen size on my notebook does not fit proberly (see attached file)
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

Best regards

Marcel

Chris-Annin, 2018-04-04:
yes it is the windows display zoom setting.  see screenshot in software folder called display setting.

Closed 2018-04-04.

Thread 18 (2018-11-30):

Great work, I have a question on 3d print version.

xuanmumy, 2018-11-30:
Hello Chris,
 Thanks for your great job, especially the assemble document, it is very clear.
 Now I'm planning to make one, I can only make a 3d print version, and I have some questions.
 did you used 3d printed j2 spindle ,j3 spindle and j6 drive post on your plastic version?
 if so, what material did you used, pla or abs?
 is it strong enough to use pla? I only have pla filament in hand currently.

aasteven, 2018-11-30:
Hi xuanmumy,
  I printed all in PLA, but I broke J6 drive post and J3 spindle first because I was doing my first test with calibration and second, the part was infilled at 20% so, I re-printed thoses 2 parts with 80 infill and re-builded the robot arm. I'm still testing.

For some parts I had to re-print the part smaller 5,10% to fit the berings (Prusa i3 MK3), if not use the dremel to reduce the size.

tks
And thanks again to Chris Annin for all is work.

xuanmumy, 2018-12-07:
> .

really? I am printing these parts at 100% infill.  I will double check my parts' size. I didn't measure them yet. bearings and electrical are on the road.

xuanmumy, 2018-12-07:
Thanks for reply, I have printed J6 drive by 100% infill, it looks good. hope it can hold on.
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

Closed 2019-07-05.

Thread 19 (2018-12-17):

Trave Track limit switch

Margoz, 2018-12-17:
Cant find it in wiring shematic, would be possible to implement and also in the homing routine?

Chris-Annin, 2018-12-17:
The travel tack is currently manually calibrated with the table up to its hard stop.  It is possible to add it to the auto calibration routine, it’s something I haven’t done yet.

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

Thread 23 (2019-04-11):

Excel bug?

xoxota99, 2019-04-11:
In the Kinematic Model excel file, Cell Q8 refers to Cell B8, which is a Forward Kinematic input (J5 Angle). Shouldn't everything in the "Forward kinematics" section (other than DH Params, tool frame and world frame) be irrelevant to the IK section?

xoxota99, 2019-04-11:
..And J4 IK solution somehow depends on J5? (Maybe this is normal? I'm not so good with the maths.)

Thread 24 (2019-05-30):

5 axis downgrade

zdenek-onz, 2019-05-30:
Hello, I'm sorry for the stupid question. I'm new here and in control robot arm. It is possible to use this software for a 5-axis robot arm. Or can the 6th axis be disabled in the software? Thank you very much for your answer. Zdenek, Brno, CZ

Chris-Annin, 2019-05-31:
The software is not directly setup for 5 axis control but it will work if
setup correctly - please see this video
https://www.youtube.com/watch?v=pcDfwlcmldE

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

airgoing, 2020-12-06:
Hi Chris Annin, if the [stepper motor](https://www.motiongoo.com/digital-stepper-driver-10a-42a-20-50vdc-for-nema-17-23-24-stepper-motor) driver can be work for AR2
https://www.motiongoo.com/digital-stepper-driver-10a-42a-20-50vdc-for-nema-17-23-24-stepper-motor
Thanks a lot!

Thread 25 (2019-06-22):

Customer 6 axis robotic arm

qweasdzcx123, 2019-06-22:
hello I have my own 6axis robotic arm,I put my DH parameter in AR2 calibration,it can move JX and xyz Coordinate。But when i only try move the X,i find that the robotic arm  will be raise.I have watch your youtube,you have the similar video,but the for J4-J6 DH parameter is not clear. I guess that my DH parameter is wrong.but i can't find where is wrong.I will appreciate that you can help me.

longqua69, 2021-02-09:
Hello,
Could you please show your error more detail? I think I can help you if I get your D-H table and its parameter.
Hope to get your respond.

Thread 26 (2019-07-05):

About step motor voltage.

xuanmumy, 2019-07-05:
Hi Chris,
    I noticed in Electrical Enclusure.pdf, you choose  DM542T for axis 6 and DM320T for axis 4.
as I googled, spec of 11hs20-0674s-pg14 , operating voltage is 6.2V , and for 14hs13-0804s-pg19,  operating voltage is 5.5V, is it ok to apply 18~24V to them?

Closed 2019-07-05.

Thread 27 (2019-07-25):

monoprice speaker wire + aviation plugs mystery

i-make-robots, 2019-07-25:
Hi!

I see in the wiring harness documentation it states to get 20 avaiation plugs and 100ft of 18ga speaker wire.  Later in the document it shows where to attach one side of the plugs.  I don't see any mention of the other end or the speaker wire.  What am I missing?  I got similar cable and plugs to put together here and they are proving very hard to assemble.

Thanks!

i-make-robots, 2019-07-25:
nm, I am blind.  Still... no idea how you did it.  You make it look easy :)

Chris-Annin, 2019-07-25:
6 plugs are installed in small black enclosure on robot (wiring harness).
6 plugs are installed in electrical enclosure (electrical enclosure
manual).  Then 6 extension cables are fabricated (connectors at each end)
to go between the robot (small black enclosure) and the main electrical
enclosure.  Let me know if that makes sense.  Im in the process of
rewriting the manual and consolidating from 3 separate manuals into one
large manual so hopefully there will be less confusion on the aviation
plugs which are called for in each manual.

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

i-make-robots, 2019-07-26:
I might need a video of your avaiation cable assembly process. We could not get the plug exterior over the cable sleeve to make room while soldering.

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

Closed 2019-07-25.

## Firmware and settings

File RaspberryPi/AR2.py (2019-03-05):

#!/usr/bin/python2.7

##########################################################################
## Version 2.1.5 #########################################################
##########################################################################
""" AR2 - Stepper motor robot control software
    Copyright (c) 2017, Chris Annin
    All rights reserved.

    You are free to share, copy and redistribute in any medium
    or format.  You are free to remix, transform and build upon
    this material.

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
    THIS SOFTWARE IS PROVIDED BY THE COPYRIGHT HOLDERS AND CONTRIBUTORS "AS IS" AND
    ANY EXPRESS OR IMPLIED WARRANTIES, INCLUDING, BUT NOT LIMITED TO, THE IMPLIED
    WARRANTIES OF MERCHANTABILITY AND FITNESS FOR A PARTICULAR PURPOSE ARE
    DISCLAIMED. IN NO EVENT SHALL CHRIS ANNIN BE LIABLE FOR ANY
    DIRECT, INDIRECT, INCIDENTAL, SPECIAL, EXEMPLARY, OR CONSEQUENTIAL DAMAGES
    (INCLUDING, BUT NOT LIMITED TO, PROCUREMENT OF SUBSTITUTE GOODS OR SERVICES;
    LOSS OF USE, DATA, OR PROFITS; OR BUSINESS INTERRUPTION) HOWEVER CAUSED AND
    ON ANY THEORY OF LIABILITY, WHETHER IN CONTRACT, STRICT LIABILITY, OR TORT
    (INCLUDING NEGLIGENCE OR OTHERWISE) ARISING IN ANY WAY OUT OF THE USE OF THIS
    SOFTWARE, EVEN IF ADVISED OF THE POSSIBILITY OF SUCH DAMAGE.

    chris.annin@gmail.com
"""
##########################################################################
##########################################################################
''' VERSION 2.1.1 CHANGES
CHANGED ALL DELAYS TO 0.05
ADDED CALIBRATE TO MID RANGE FUNCTION
REMOVED CALIBRATE WRITE FROM CALIBRATE ROUTINE - USES SavePosData
CHANGED E65 = TO J15
ajusted axis limits for DM542T
RE-WRITE OF MOVE SYNC ALGORITHM
VERSION 2.1.4 CHANGES
POSITIONS BY CARTISIAN INSTEAD OF STEP COUNT
ADDED STORED POSITIONS
ADDED 7TH AXIS TRAVEL TRACK
ADDED BASIC VISION
CHANGED INCREMENT TO ++ AND DECREMENT TO --
VERSION 2.1.5 CHANGES
CHANGES KINEMATICS FOR WRIST ORIENTATION J4-J6
SPEED UP CALIBRATION MOVE
'''
##########################################################################

from Tkinter import *
import pickle
import serial
import time
import threading
import Queue
import math
import ttk
import tkMessageBox
import webbrowser



root = Tk()
root.wm_title("AR2 software 1.5")
#root.iconbitmap(r'AR2.ico')
root.resizable(width=True, height=True)
root.geometry('1280x720+0+0')
root.attributes('-zoomed',True)

root.runTrue = 0

nb = ttk.Notebook(root, width=1280, height=635)
nb.place(x=0, y=0)

tab1 = ttk.Frame(nb)
nb.add(tab1, text=' Main Controls ')

tab2 = ttk.Frame(nb)
nb.add(tab2, text='  Calibration  ')

tab3 = ttk.Frame(nb)
nb.add(tab3, text=' Inputs Outputs ')

tab4 = ttk.Frame(nb)
nb.add(tab4, text='   Registers    ')

tab5 = ttk.Frame(nb)
nb.add(tab5, text='   Vision    ')

global J1NegAngLim
global J1PosAngLim
global J1StepLim
global J1DegPerStep
global J1StepCur
global J1AngCur
global J2NegAngLim
global J2PosAngLim
global J2StepLim
global J2DegPerStep
global J2StepCur
global J2AngCur
global J2NegAngLim
global J2PosAngLim
global J2StepLim
global J2DegPerStep
global J2StepCur
global J2AngCur
global J3NegAngLim
global J3PosAngLim
global J3StepLim
global J3DegPerStep
global J3StepCur
global J3AngCur
global J4NegAngLim
global J4PosAngLim
global J4StepLim
global J4DegPerStep
global J4StepCur
global J4AngCur
global J5NegAngLim
global J5PosAngLim
global J5StepLim
global J5DegPerStep
global J5StepCur
global J5AngCur
global J6NegAngLim
global J6PosAngLim
global J6StepLim
global J6DegPerStep
global J6StepCur
global J6AngCur
global XcurPos
global YcurPos
global ZcurPos
global RxcurPos
global RycurPos
global RzcurPos
global TrackcurPos
global TrackLength
global TrackStepLim

## Wrist Congig
global WC


###Fwd Kinamatic outputs
global H4
global H5
global H6
global H7
global H8
global H9

###Fwd Kinamatic rotation matrix
global G60
global G61
global G62
global H60
global H61
global H62
global I60
global I61
global I62

###Orientation
global E7
global E8
global E27
global E28


global DHr1
global DHr2
global DHr3
global DHr4
global DHr5
global DHr6

global DHa1
global DHa2
global DHa3
global DHa4
global DHa5
global DHa6

global DHd1
global DHd2
global DHd3
global DHd4
global DHd5
global DHd6

global DHt1
global DHt2
global DHt3
global DHt4
global DHt5
global DHt6


###jog step options
global JogStepsStat
JogStepsStat = IntVar()


###DEFS###################################################################
##########################################################################


def setCom():
  global ser
  port = "/dev/ttyACM0" #+ comPortEntryField.get()
  baud = 9600
  ser = serial.Serial(port, baud)

def deleteitem():
  selRow = tab1.progView.curselection()[0]
  selection = tab1.progView.curselection()
  tab1.progView.delete(selection[0])
  tab1.progView.select_set(selRow)
  value=tab1.progView.get(0,END)
  pickle.dump(value,open("/home/pi/Documents/AR2/RaspberryPi/"+ProgEntryField.get(),"wb"))
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

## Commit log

2018-08-23 Add files via upload
    added information on gripper wiring
2018-08-26 Add files via upload
    added belt tension note for J4 motor
2018-10-27 Add files via upload
    added 3mm rod info
2019-01-01 Custom PCB Shield
    This custom PCB is a shield for the Arudino Mega. It takes 24V from the power supply (I included 2 holes below the solder pads to zip tie the wires in place) and uses 2 DC-DC step-down converters (ht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
